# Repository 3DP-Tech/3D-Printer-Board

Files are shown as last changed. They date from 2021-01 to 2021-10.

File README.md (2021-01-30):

# 3D-Printer-Board
Check out my [3DP Tech You Tube channel](https://www.youtube.com/playlist?list=PLOfiVhkRK3Go6M8yRqPx5GOqqJWyXBp_2). This repository contains support files for the "Build a 3D Printer Control Board" series.

In this video series I explore the electronics of a 3D printer. I review the components that make up the control board and explain how they interact with the firmware to control a 3D printer. Finally, I show you how to build a complete control board for a 3D printer on a solderless breadboard.
## Episode Index
### Episode 1 - Introduction
In this episode I review the electronic components found in a 3D printer and give a high-level description of the role each plays to accomplish the task of printing a 3D model. I give an overview of the remaining episodes and state the objectives of the series.
### Episode 2 - Arduino Core
In this episode I demonstrate how to build a basic Arduino microcontroller on a breadboard. I guide you through the minimum circuit components required to get an ATMEGA1284P based Arduino up and running.
### Episode 3 - Flashing the Bootloader
In this episode I demonstrate how to flash a bootloader to the Arduino core circuit built in episode 2. This will allow firmware to be flashed easily from the Arduino IDE using a serial port.
### Episode 4 - Adding USB Support
In this episode I demonstrate a few ways to connect to the microcontroller using the USB port on a computer. I also demonstrate how to add a permanent USB port to the breadboard.
### Episode 5 - Power Supply
In this episode I demonstrate how to add a 5V regulator to the breadboard so that the control board can be run from a 12V or 24V power supply. I discuss the various ways to power the board while building it and cover the reason why a 12V or 24V power supply is necessary.
### Episode 6 - Stepper Motors
In this episode I review the basics of a stepper motor and demonstrate how to drive a stepper motor from an Arduino. I walk through adding the four necessary stepper motor drivers needed for the 3D printer.
### Episode 7 - Hot End, Bed Heater and Fan
In this episode I demonstrate how to control high voltage and high current devices through a MOSFET and an Arduino PWM pin. I discuss the basic principle of PWM and add the circuits to our breadboard that will control the fans, the hot bed heater the hot end heater cartridge.
### Episode 8 - Thermistors
In this episode I describe the basic operation of a thermistor and show how to read temperature. I walk through adding the necessary thermistor circuits to read temperatures on the 3D printer.
### Episode 9 - End Stops
In this episode I review the basics of monitoring a push button. I demonstrate how to add the end stop circuits to the printer control board.
### Episode 10 - LCD
In this episode I walk through the LCD used on the 3D printer and demonstrate how to add it to the control board.
### Episode 11 - Encoder & Piezo Buzzer
In this episode I demonstrate the basic function of the rotary encoder used to make menu selections on the LCD. I'll also show how to wire it into the breadboard along with the piezo buzzer (or beeper) to add (very) basic sound.
### Episode 12 - MicroSD Card
In this episode I demonstrate how to add a MicroSD card reader to the control board.
### Episode 13 - Flashing Marlin
In this episode I walk through configuring Marlin firmware for the control board and demonstrate how to flash it through the Arduino IDE. I also demonstrate the firmware operation on the control board using a virtual/demo 3D printer.
### Episode 14 - Connecting a Printer
In this episode I will connect the breadboard based control board to an actual 3D printer and print a 3D model.
### Episode 15 - Expanding the Board
In this episode I demonstrate ways to expand the board to offer more options that are readily supportable in the Marlin firmware.

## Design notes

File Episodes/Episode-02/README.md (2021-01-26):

# Episode 2 - Arduino Core
This folder contains supporting files for Episode 2.

## Arduino as ISP
Here is the reference to using the Arduino as a programmer.

[Arduino as ISP and Arduino Bootloaders](https://www.arduino.cc/en/pmwiki.php?n=Tutorial/ArduinoISP)

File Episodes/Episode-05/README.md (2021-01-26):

# Episode 5 - Power Supply
This folder contains supporting files for the episode.

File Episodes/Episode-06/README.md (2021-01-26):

# Episode 6 - Stepper Motors
This folder contains supporting files for the episode.

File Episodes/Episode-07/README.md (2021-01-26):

# Episode 7 - Hot End, Bed Heater and Fan
This folder contains supporting files for the episode.

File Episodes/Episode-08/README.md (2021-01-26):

# Episode 8 - Thermistors
This folder contains supporting files for the episode.

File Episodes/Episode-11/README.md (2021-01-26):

# Episode 11 - Encoder & Piezo Buzzer
This folder contains supporting files for the episode.

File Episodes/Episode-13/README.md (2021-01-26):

# Episode 13 - Flashing Marlin
This folder contains supporting files for the episode.

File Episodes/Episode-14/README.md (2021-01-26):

# Episode 14 - Connecting a Printer
This folder contains supporting files for the episode.

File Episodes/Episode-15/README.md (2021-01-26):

# Episode 15 - Expanding the Board
This folder contains supporting files for the episode.

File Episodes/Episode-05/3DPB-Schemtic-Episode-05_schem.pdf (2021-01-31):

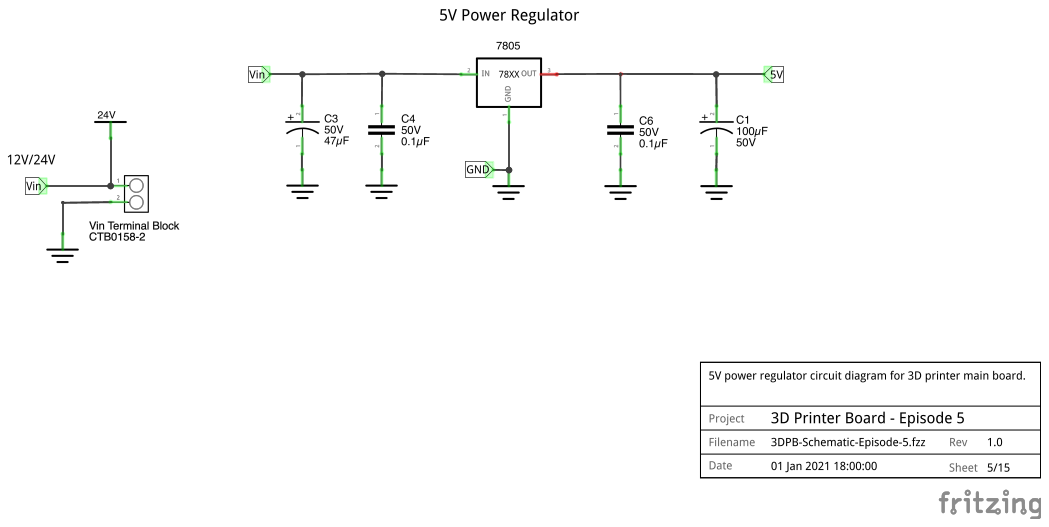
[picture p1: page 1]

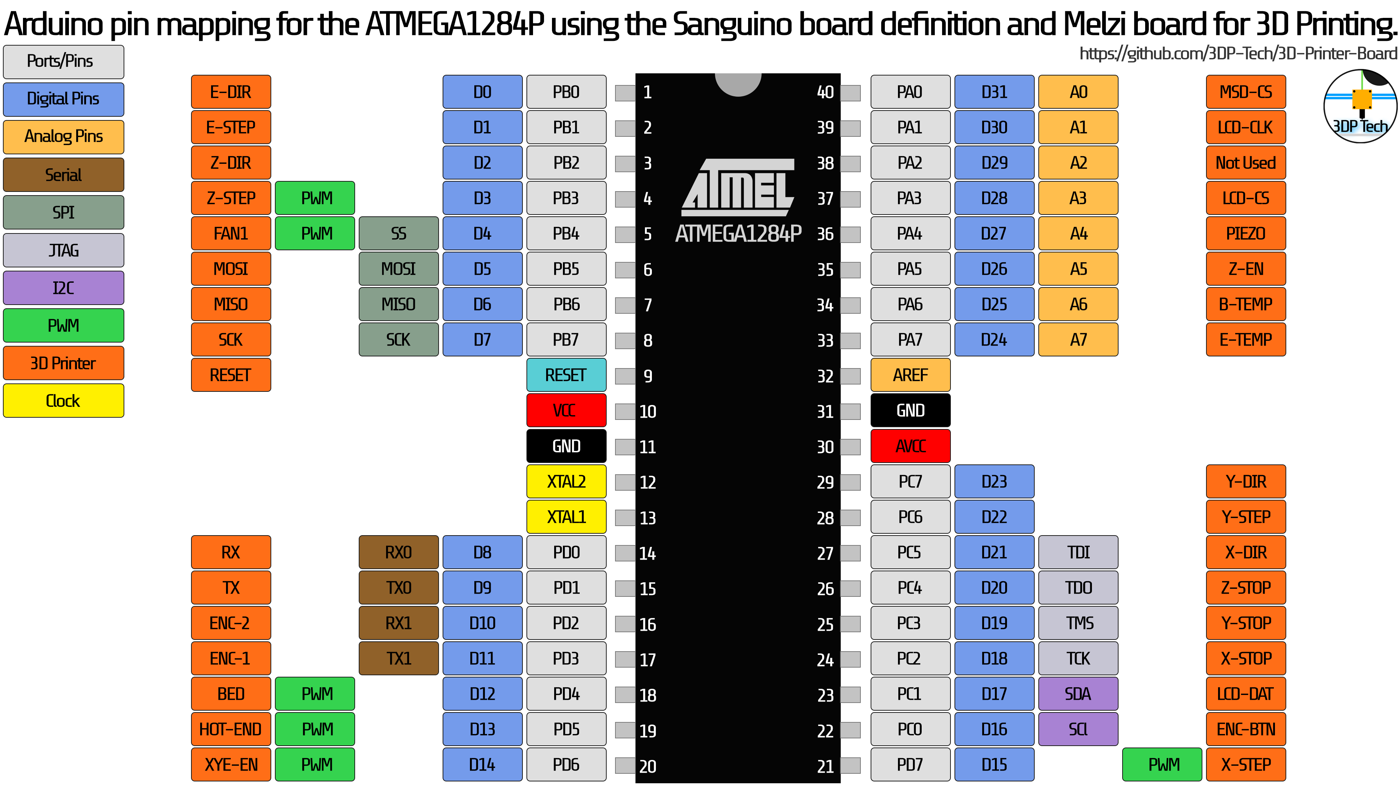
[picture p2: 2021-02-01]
Extras/ATMega1284P-Pins.png

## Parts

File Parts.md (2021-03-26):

# Obtaining Parts and Tools
The products used in this episode are listed below along with at least one source link.

Hopefully you have much of the items on this list already. If you try to purchase everything the cost will be very high. I include the complete list of items I use but I also show ways to get around not having some of these items.

> All parts that are referenced from Adafruit can be ordered directly from this list:
> [Adafruit Wishlist](http://www.adafruit.com/wishlists/517409)

> All of the parts referenced from Amazon can be ordered directly from this list:  [Amazon Wishlist](https://www.amazon.com/ideas/amzn1.account.AHJPQKIYOSU7VLCNUL2MLWOG4RNA/3R3GTU77Y6I2H)

# Parts List and Source
## All Episodes
### Tools
There are a couple of tools that are necessary. A pair of side/diagonal cutters, a pair of wire strippers and a pair of needle-nose pliers. Optionally you may need a soldering iron. I highly recommend a good one, but there are so many to choose from. Below are links to recommended products but you can find suitable alternatives if you like.

* [Flush diagonal cutters](https://www.adafruit.com/product/527)
* [Wire Strippers](https://www.adafruit.com/product/527)
* [Simple pliers](https://www.adafruit.com/product/527)
* [Digital Genuine Hakko FX-888D](https://www.adafruit.com/product/527)

### Large Solderless Breadboard
The large board I am using was purchased from Adafruit ([https://www.adafruit.com/product/443](https://www.adafruit.com/product/443)). If you do not want to purchase this board, or you already have some breadboards, you can just take three breadboards and lock them together. Good quality boards can be purchased from Amazon as well ([https://www.amazon.com/gp/product/B07FY9LQJF](https://www.amazon.com/gp/product/B07FY9LQJF)).

### Hook-up Wire Spool Set
It is nice to have a set of hook-up wire suitable for a breadboard. In the videos I cut most of the wires to length to keep the board neat and clean. 

This is solid core wire (22AWG Solid Core - 6 x 25 ft) and can be purchased from Adafruit ([https://www.adafruit.com/product/131](https://www.adafruit.com/product/1311)1), or from Amazon ([https://www.amazon.com/gp/product/B00B4ZRPEY](https://www.amazon.com/gp/product/B00B4ZRPEY)).

### Jumper Wires
In addition to cutting wires to length, it is useful to have a few pre-made jumper wires. These wll come in handy for working with the Uno to program the chip or to connect the power supply.

[https://www.adafruit.com/product/1957](https://www.adafruit.com/product/1957)
## Episode 1
No parts needed for this episode.
## Episode 2
### Adjustable Power Supply
I am using a bench top adjustable power supply for to power my mainboard through most of the episodes. There are many varieties of these at a range of prices. The power supply I am using in the videos is linked below.

[https://www.amazon.com/gp/product/B085S34NNW](https://www.amazon.com/gp/product/B085S34NNW)

### Arduino Uno
An AVR programmer is required to program the ATMEGA1284P and to load a bootloader. It is much easier to use an Arduino. The simplest board to use for this is the Uno but any 5V Arduino board will work.

[https://store.arduino.cc/usa/arduino-uno-rev3]()

### ATMEGA1284P
I ordered this directly from Microchip. The shipping was low, and it came in a few days. I recommend ordering at least 2 since these are only a few dollars.

[https://www.microchipdirect.com/product/ATMEGA1284P-PU](https://www.microchipdirect.com/product/ATMEGA1284P-PU)

### Clock Crystal
The ATMEGA1284P will be run using a 16Mhz crystal. The datasheet also calls for two 20pF capacitors. These three parts can be purchased from Adafruit in a kit.

[https://www.adafruit.com/product/2215](https://www.adafruit.com/product/2215)

### Breadboard Compatible Tactile Push Button
Adafruit sells a pack of these buttons that can be pressed into the breadboard. This package includes snap on buttons that make it easy to use the switch.

[https://www.adafruit.com/product/1009](https://www.adafruit.com/product/1009)

### 6-pin AVR ISP Breadboard Adapter
These are not required but make programming the ATMEGA1284 bootloader a little easier (and they help make the wiring easier). I recommend ordering two of these.

[https://www.adafruit.com/product/1465](https://www.adafruit.com/product/1465)

### 6-pin Socket/Socket IDC cable - 6"
This is the companion cable to the AVR ISP breadboard adapter above.

[https://www.adafruit.com/product/371](https://www.adafruit.com/product/371)

### Breadboard-friendly SPDT Slide Switch
This is optional, but this slide switch can be added to the breadboard as a power switch.

[https://www.adafruit.com/product/805](https://www.adafruit.com/product/805)

### Mini Digital DC Voltmeter
I use these to monitor the voltage on the breadboard. They are also handy to measure the output of the MOSFETs.

[https://www.amazon.com/gp/product/B0761MG9NS](https://www.amazon.com/gp/product/B0761MG9NS)

### Resistors
Resistors can be purchased up from just about anywhere. Either purchase them by size or get a variety container from Amazon (https://www.amazon.com/gp/product/B08BNDL6DS).

**Sizes Needed:**
220 Ω, 10K Ω

### Capacitors
Capacitors can be purchased from just about anywhere. Either purchase them by size or get a variety container from Amazon (https://www.amazon.com/gp/product/B08BNDL6DS).

Electrolytic: [https://www.amazon.com/gp/product/B07TWCT2ZB](https://www.amazon.com/gp/product/B07TWCT2ZB)

**Sizes needed:**
10 µF, 47 µF, 100 µF

Ceramic: [https://www.amazon.com/gp/product/B07TWBVJVN](https://www.amazon.com/gp/product/B07TWBVJVN)

**Sizes needed:**
0.1 µF, 20 pF (if you purchase the crystal without them)

### LEDs
Multiple LEDs in a variety of colors are used. It does not matter if you use the 3mm or 5mm size. I recommend at least three colors, red, green and blue. LEDs can be purchased on varitey packs or by color.

* [Diffused 5mm LED Pack - 5 LEDs each in 5 Colors - 25 Pack](https://www.adafruit.com/product/4203)
* [Super Bright Red 5mm LED (25 pack)](https://www.adafruit.com/product/297)
* [Super Bright Green 5mm LED (25 pack)](https://www.adafruit.com/product/300)
* [Super Bright Blue 5mm LED (25 pack)](https://www.adafruit.com/product/301)

## Episode 12

### Rotary Encoder
https://www.adafruit.com/product/377

### Fancy Knob
(very optional)
https://www.adafruit.com/product/2056

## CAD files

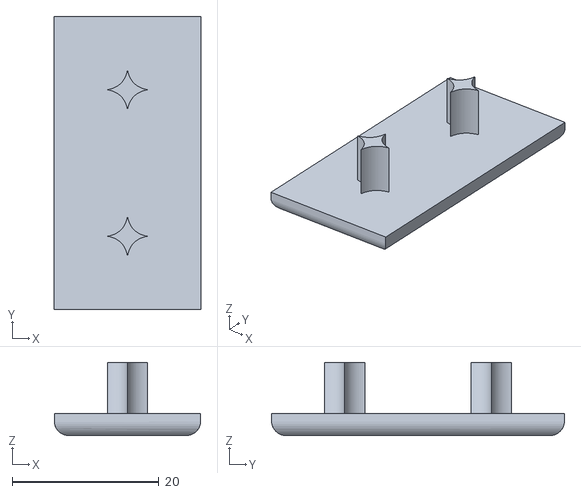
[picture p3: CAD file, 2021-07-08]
STL/Mj_End_Cap_with_pins.stl
20.0 x 40.0 x 10.0

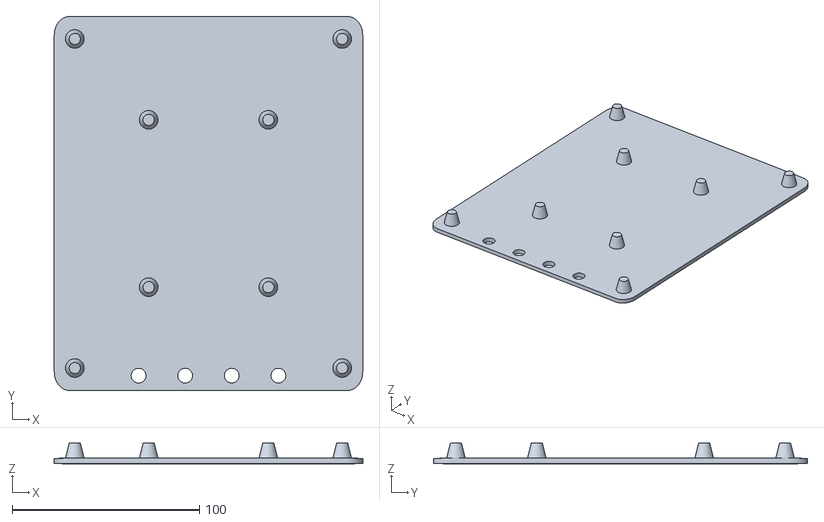
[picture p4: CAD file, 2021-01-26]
STL/Large-Breadboard-Plate.stl
165.0 x 200.0 x 11.0

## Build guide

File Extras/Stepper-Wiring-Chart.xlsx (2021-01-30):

Connector
Red | Black | Blue | Green
A | B | C | D
B+ | A+ | B- | A-
1B | 2B | 1A | 2A
Pair 1 | Pair 2 | Pair 1 | Pair 2

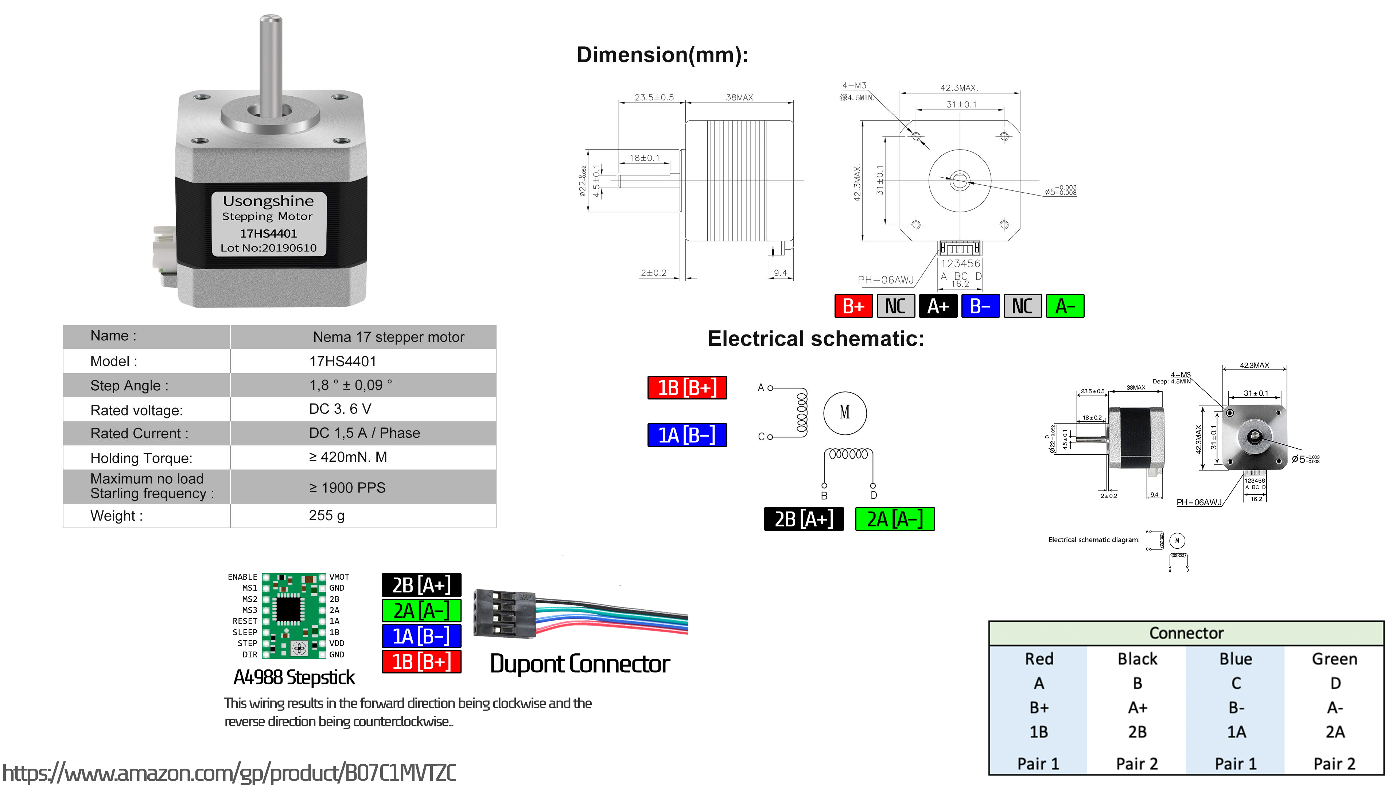
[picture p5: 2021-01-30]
Extras/Stepper-Wiring.png

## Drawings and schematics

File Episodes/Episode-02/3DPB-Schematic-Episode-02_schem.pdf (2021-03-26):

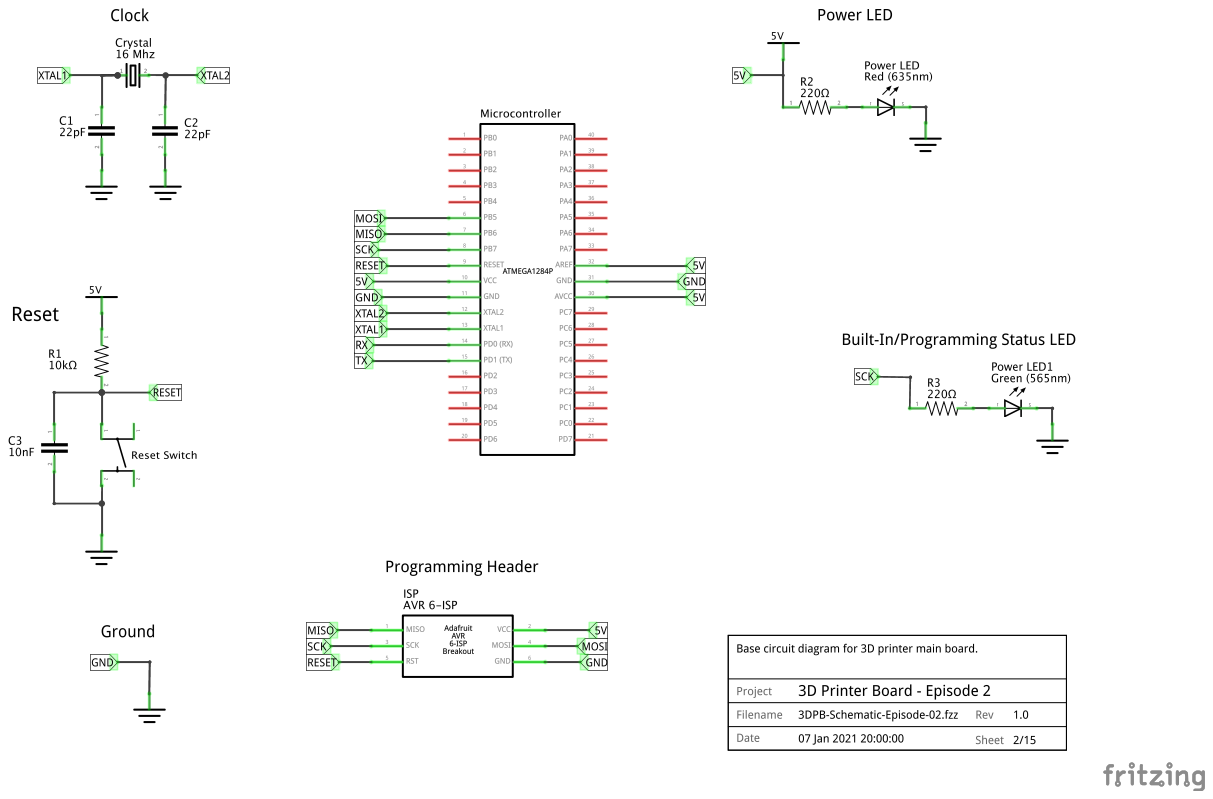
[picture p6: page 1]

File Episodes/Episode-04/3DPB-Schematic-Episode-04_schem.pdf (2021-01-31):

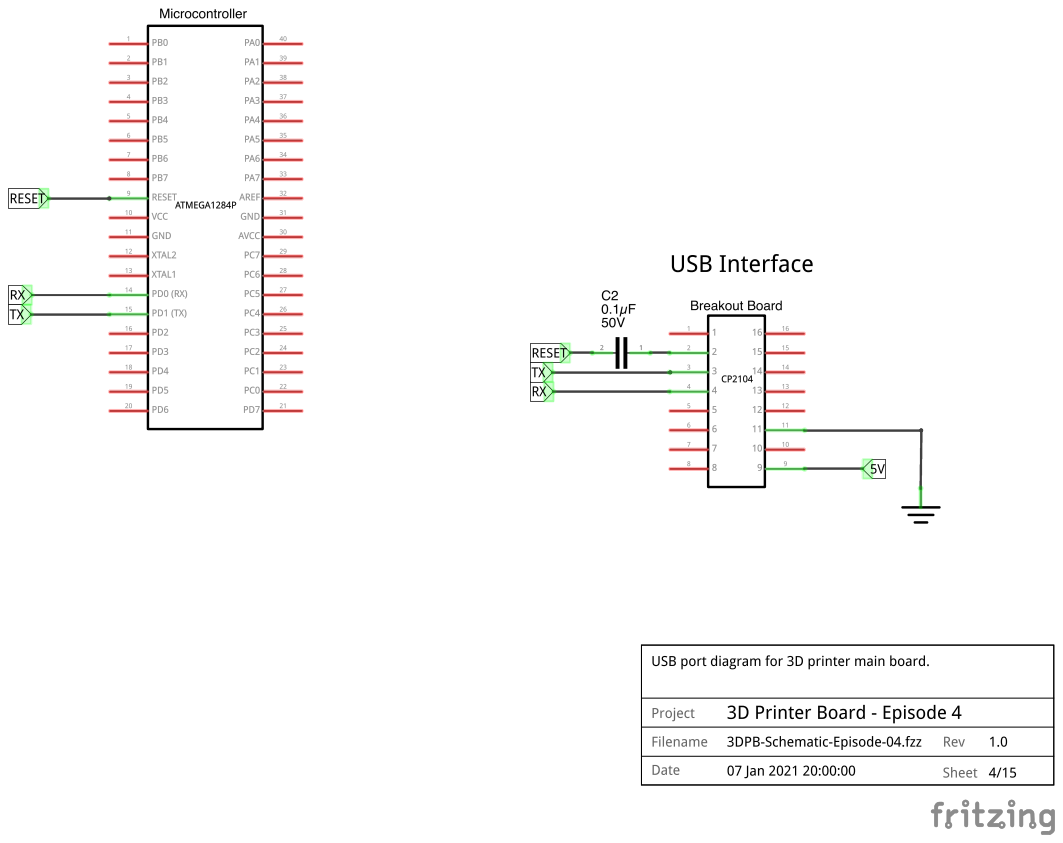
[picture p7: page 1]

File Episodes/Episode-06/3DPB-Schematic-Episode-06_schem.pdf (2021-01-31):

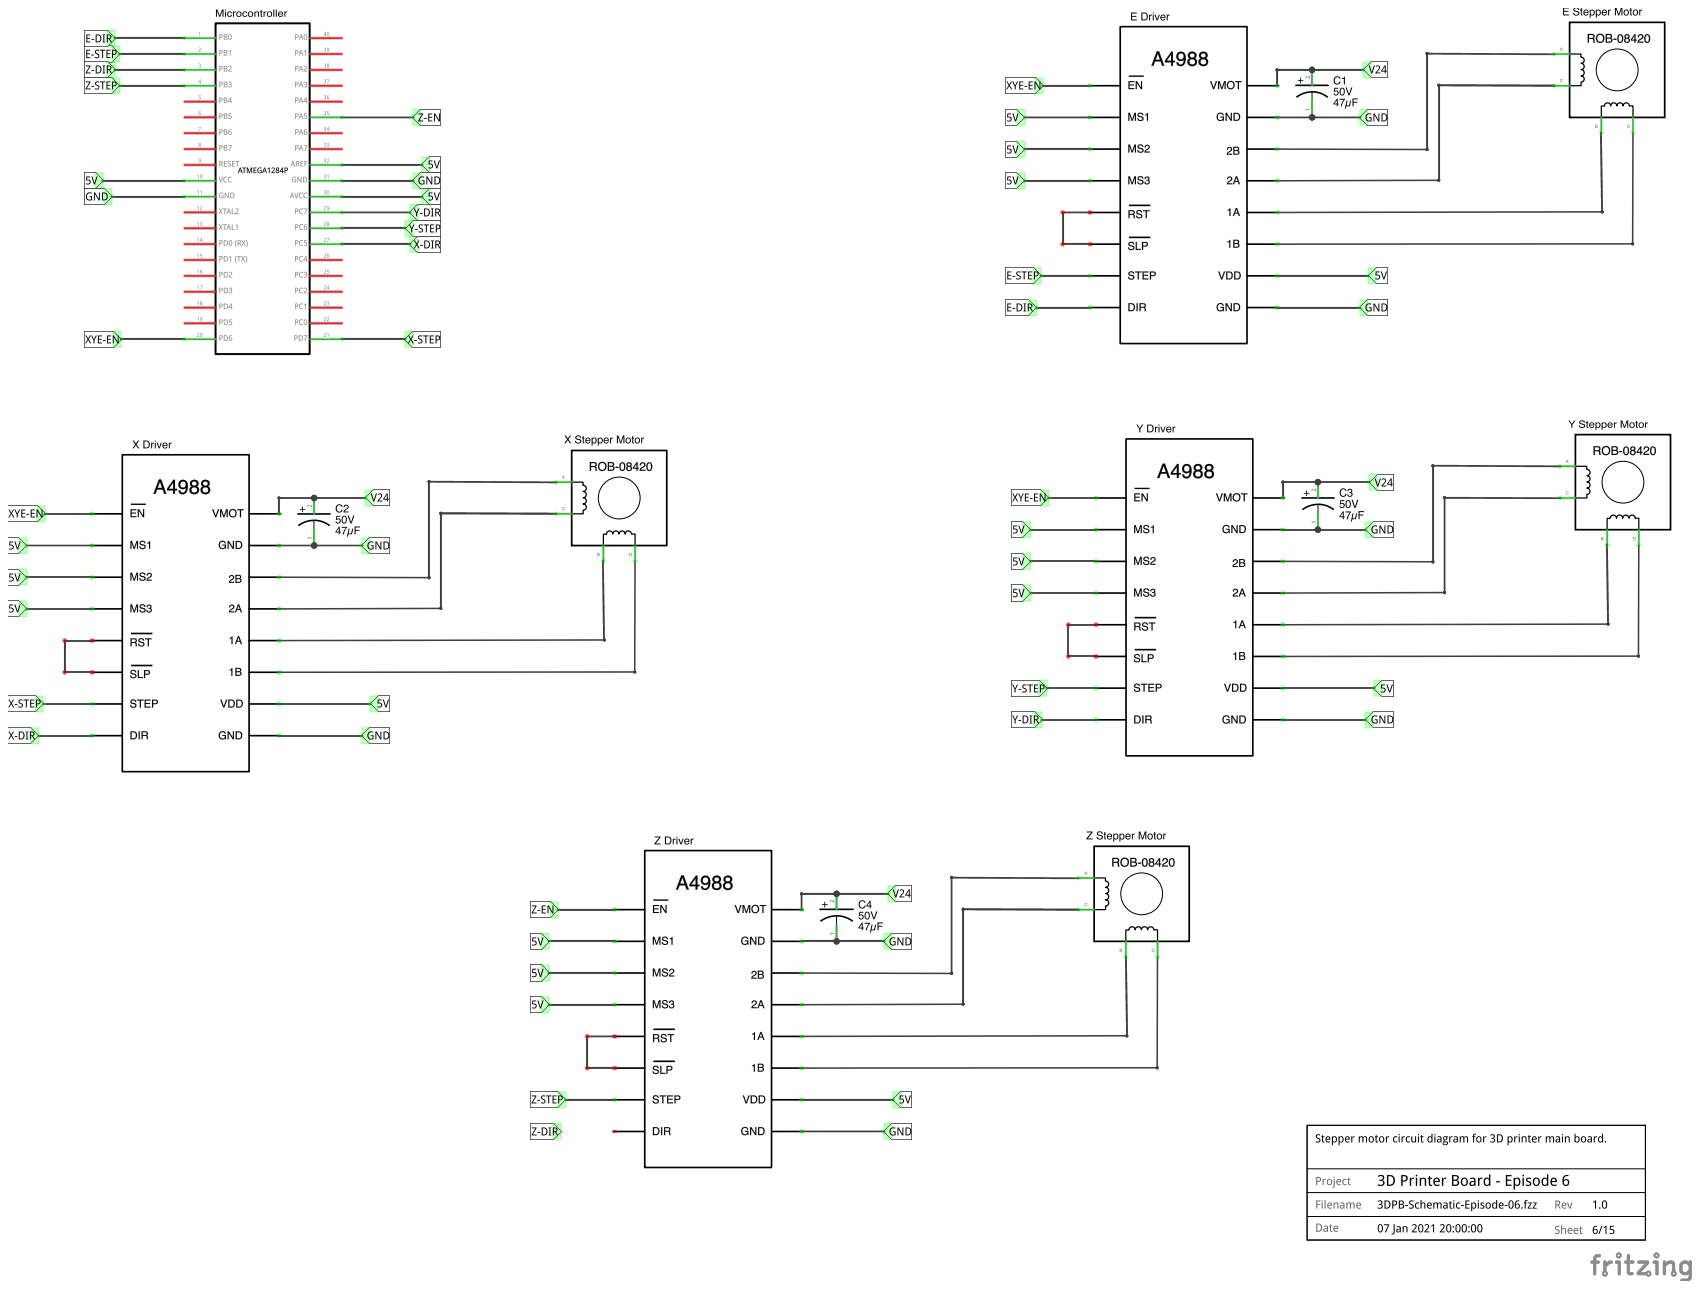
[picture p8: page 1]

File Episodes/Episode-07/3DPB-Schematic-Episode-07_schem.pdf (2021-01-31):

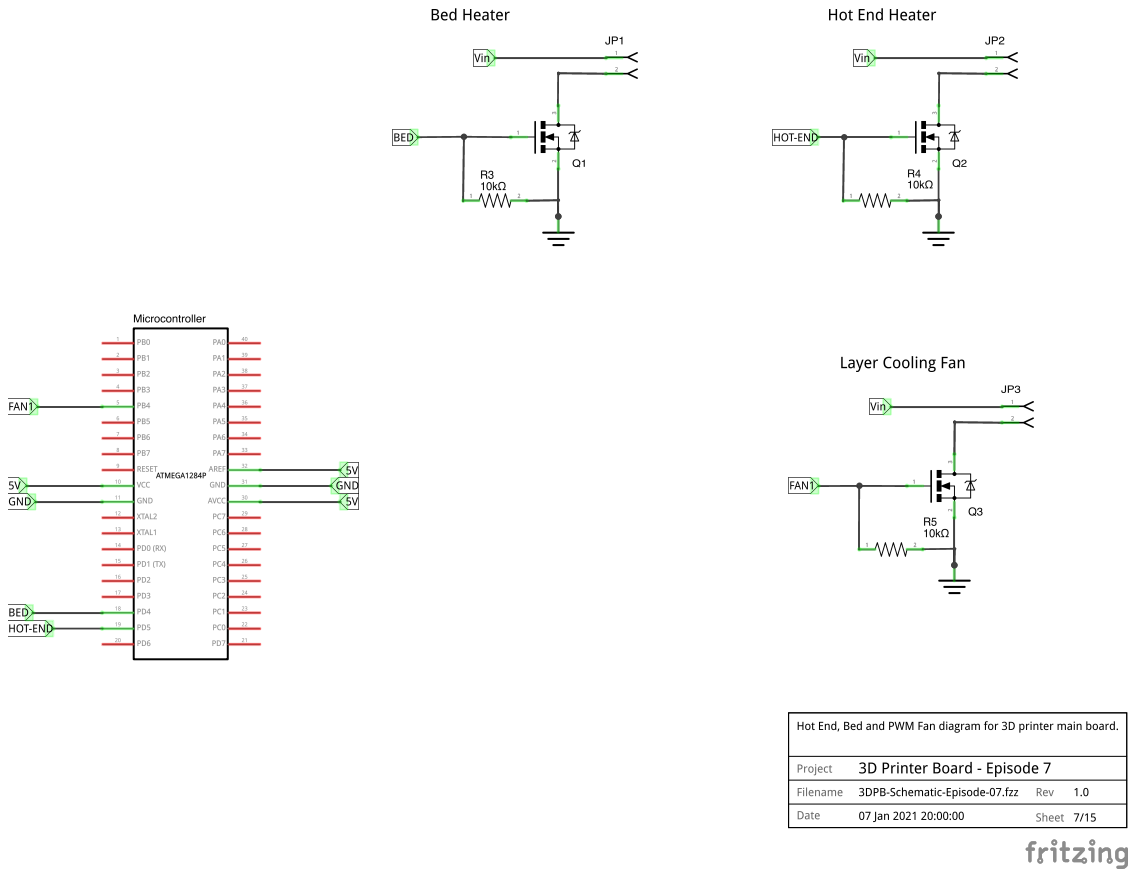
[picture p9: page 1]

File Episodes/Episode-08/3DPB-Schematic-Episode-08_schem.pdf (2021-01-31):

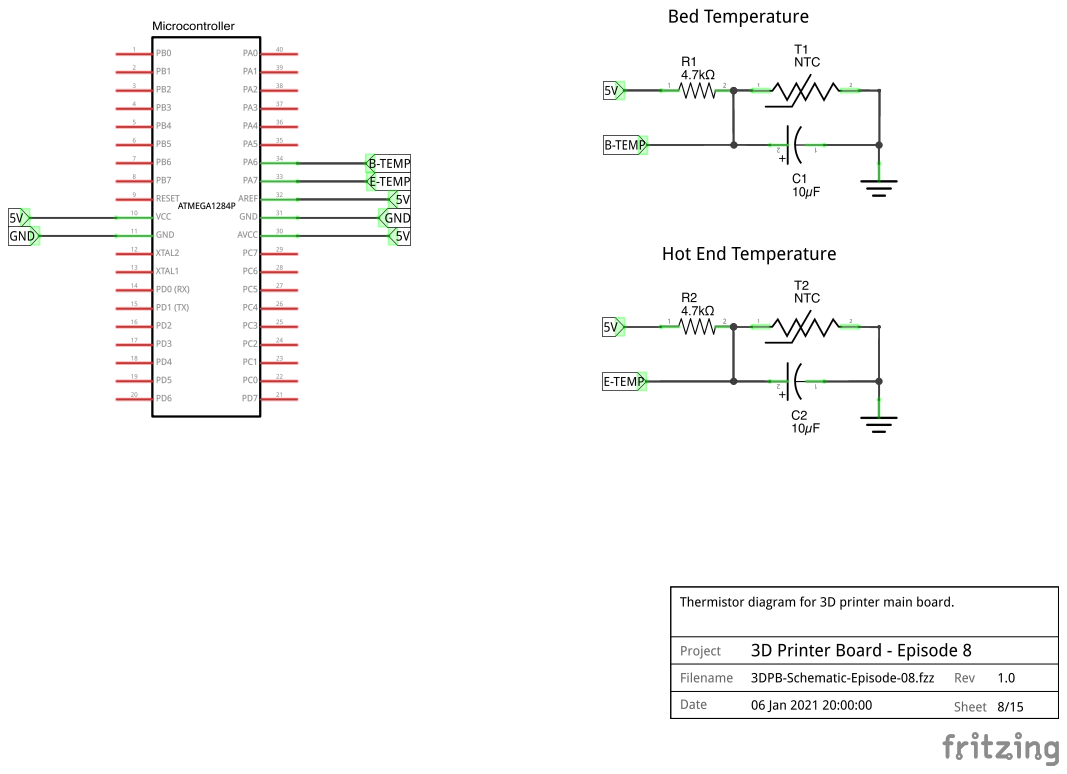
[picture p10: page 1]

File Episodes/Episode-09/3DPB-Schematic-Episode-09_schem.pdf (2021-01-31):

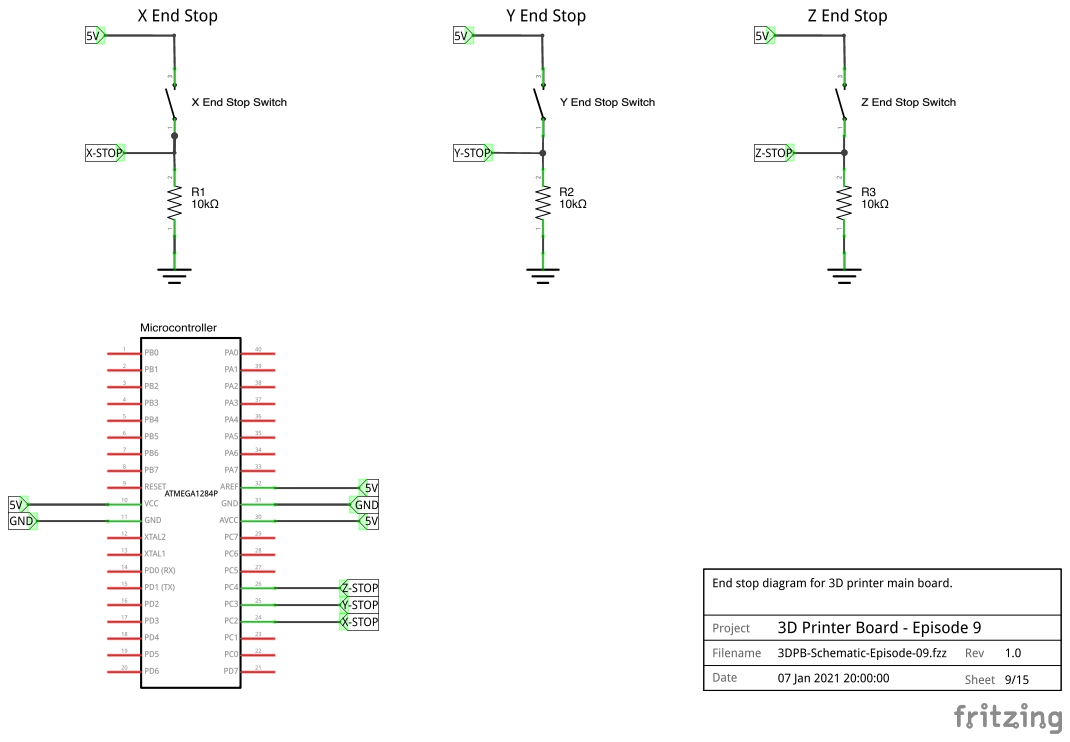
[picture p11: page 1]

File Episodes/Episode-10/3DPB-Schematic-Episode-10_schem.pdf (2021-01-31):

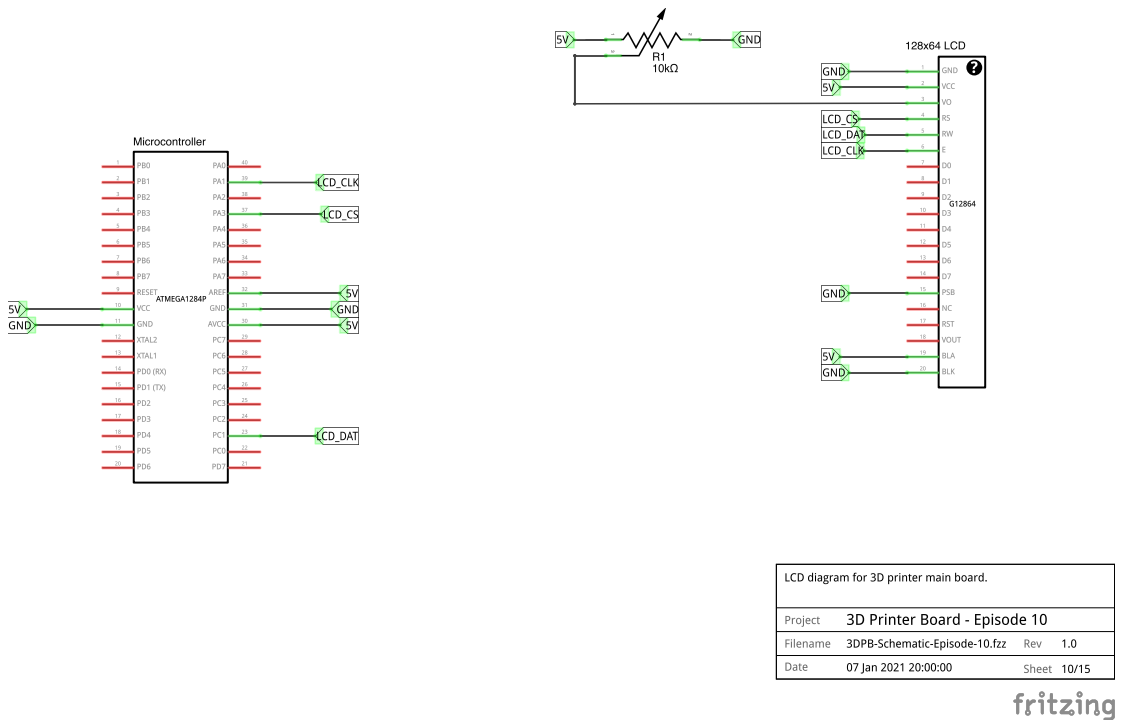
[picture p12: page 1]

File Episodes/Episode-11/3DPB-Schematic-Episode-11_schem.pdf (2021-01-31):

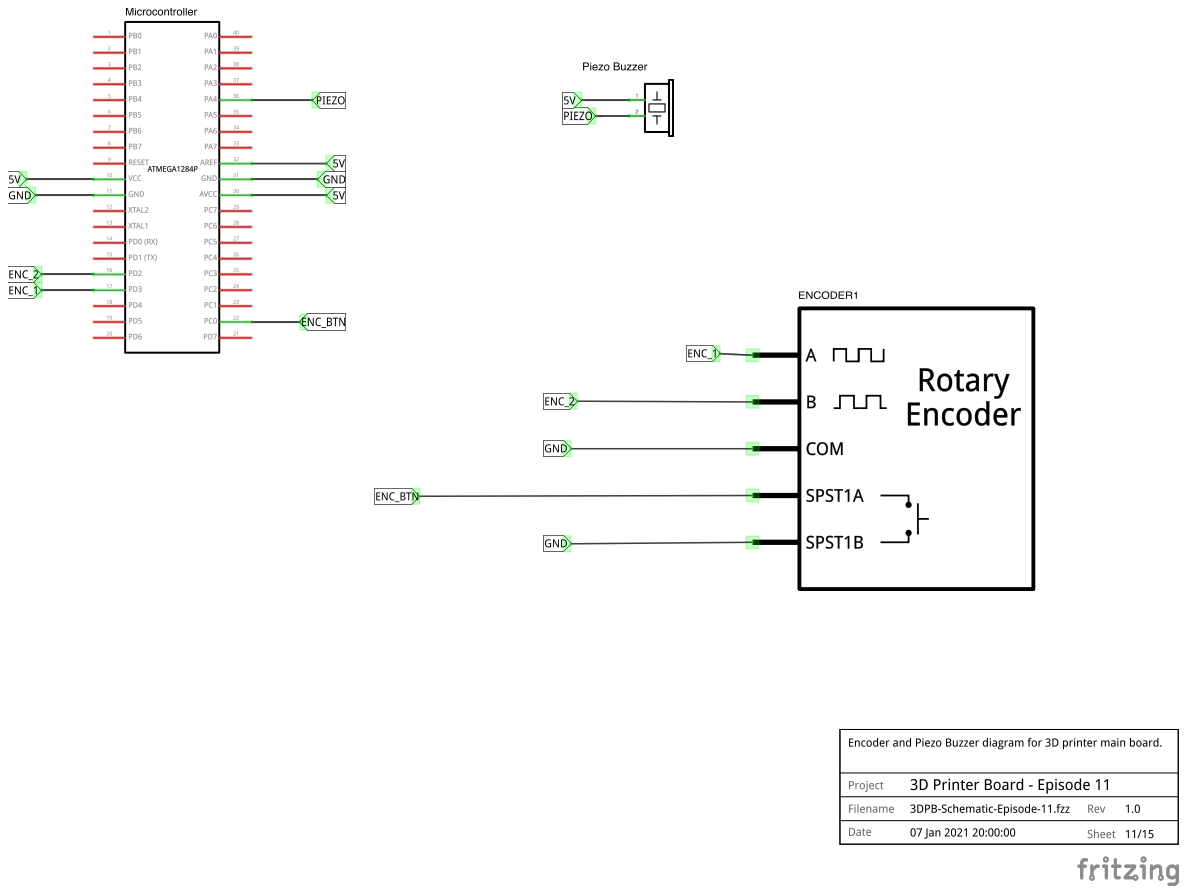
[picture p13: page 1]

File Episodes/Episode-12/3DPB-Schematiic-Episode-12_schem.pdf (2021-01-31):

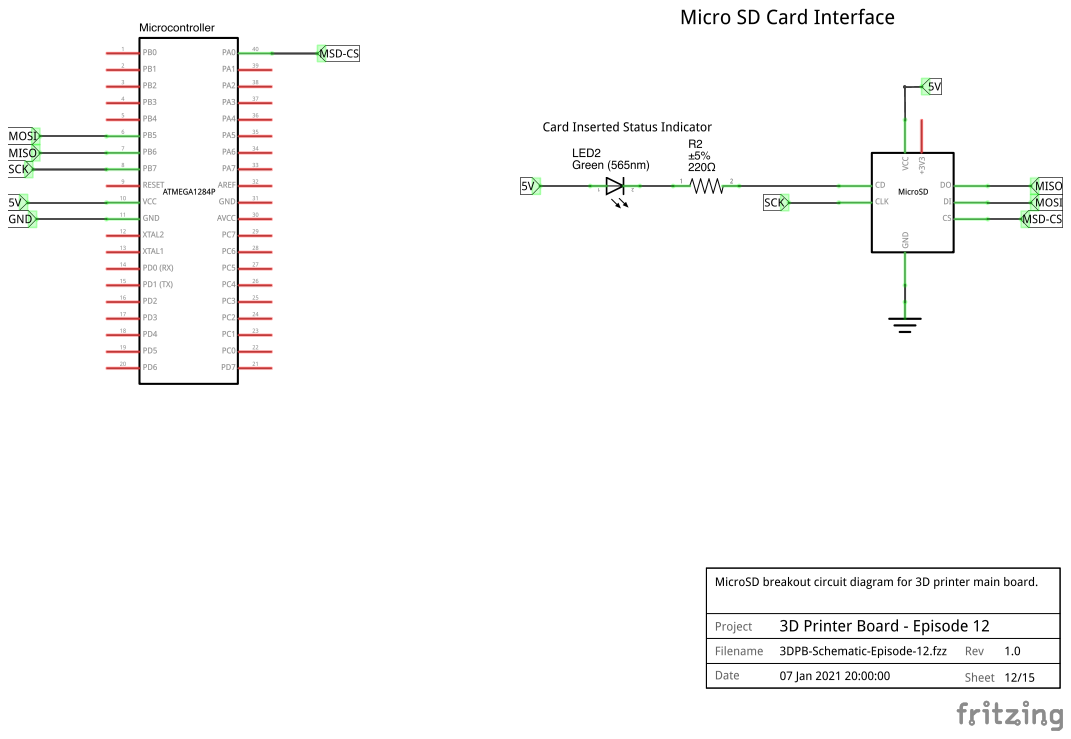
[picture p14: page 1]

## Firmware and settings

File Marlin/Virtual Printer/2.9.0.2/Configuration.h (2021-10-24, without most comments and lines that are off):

#pragma once
#define CONFIGURATION_H_VERSION 02000902
#define STRING_CONFIG_H_AUTHOR "(Daniel Porrey, 3DP-Tech)" // Who made the changes.
#define SHOW_BOOTSCREEN
#define SHOW_CUSTOM_BOOTSCREEN
#define CUSTOM_STATUS_SCREEN_IMAGE
#define SERIAL_PORT 0
#define BAUDRATE 500000
  #define MOTHERBOARD BOARD_MELZI_CREALITY
#define CUSTOM_MACHINE_NAME "V3D Printer"
#define MACHINE_UUID "3f756d04-a356-4632-ac29-15a5529378b4"
#if LINEAR_AXES >= 4
  #define AXIS4_NAME 'A' // :['A', 'B', 'C', 'U', 'V', 'W']
#endif
#if LINEAR_AXES >= 5
  #define AXIS5_NAME 'B' // :['A', 'B', 'C', 'U', 'V', 'W']
#endif
#if LINEAR_AXES >= 6
  #define AXIS6_NAME 'C' // :['A', 'B', 'C', 'U', 'V', 'W']
#endif
#define EXTRUDERS 1
#define DEFAULT_NOMINAL_FILAMENT_DIA 1.75
#define TEMP_SENSOR_0 1
#define TEMP_SENSOR_1 0
#define TEMP_SENSOR_2 0
#define TEMP_SENSOR_3 0
#define TEMP_SENSOR_4 0
#define TEMP_SENSOR_5 0
#define TEMP_SENSOR_6 0
#define TEMP_SENSOR_7 0
#define TEMP_SENSOR_BED 1
#define TEMP_SENSOR_PROBE 0
#define TEMP_SENSOR_CHAMBER 0
#define TEMP_SENSOR_COOLER 0
#define TEMP_SENSOR_BOARD 0
#define TEMP_SENSOR_REDUNDANT 0
#define DUMMY_THERMISTOR_998_VALUE  25
#define DUMMY_THERMISTOR_999_VALUE 100
#define TEMP_RESIDENCY_TIME         10  // (seconds) Time to wait for hotend to "settle" in M109
#define TEMP_WINDOW                  1  // (°C) Temperature proximity for the "temperature reached" timer
#define TEMP_HYSTERESIS              3  // (°C) Temperature proximity considered "close enough" to the target
#define TEMP_BED_RESIDENCY_TIME     10  // (seconds) Time to wait for bed to "settle" in M190
#define TEMP_BED_WINDOW              1  // (°C) Temperature proximity for the "temperature reached" timer
#define TEMP_BED_HYSTERESIS          3  // (°C) Temperature proximity considered "close enough" to the target
#define TEMP_CHAMBER_RESIDENCY_TIME 10  // (seconds) Time to wait for chamber to "settle" in M191
#define TEMP_CHAMBER_WINDOW          1  // (°C) Temperature proximity for the "temperature reached" timer
#define TEMP_CHAMBER_HYSTERESIS      3  // (°C) Temperature proximity considered "close enough" to the target
#if TEMP_SENSOR_REDUNDANT
  #define TEMP_SENSOR_REDUNDANT_SOURCE    E1  // The sensor that will provide the redundant reading.
  #define TEMP_SENSOR_REDUNDANT_TARGET    E0  // The sensor that we are providing a redundant reading for.
  #define TEMP_SENSOR_REDUNDANT_MAX_DIFF  10  // (°C) Temperature difference that will trigger a print abort.
#endif
#define HEATER_0_MINTEMP   5
#define HEATER_1_MINTEMP   5
#define HEATER_2_MINTEMP   5
#define HEATER_3_MINTEMP   5
#define HEATER_4_MINTEMP   5
#define HEATER_5_MINTEMP   5
#define HEATER_6_MINTEMP   5
#define HEATER_7_MINTEMP   5
#define BED_MINTEMP        5
#define CHAMBER_MINTEMP    5
#define HEATER_0_MAXTEMP 275
#define HEATER_1_MAXTEMP 275
#define HEATER_2_MAXTEMP 275
#define HEATER_3_MAXTEMP 275
#define HEATER_4_MAXTEMP 275
#define HEATER_5_MAXTEMP 275
#define HEATER_6_MAXTEMP 275
#define HEATER_7_MAXTEMP 275
#define BED_MAXTEMP      125
#define CHAMBER_MAXTEMP  60
#define HOTEND_OVERSHOOT 15   // (°C) Forbid temperatures over MAXTEMP - OVERSHOOT
#define BED_OVERSHOOT    10   // (°C) Forbid temperatures over MAXTEMP - OVERSHOOT
#define COOLER_OVERSHOOT  2   // (°C) Forbid temperatures closer than OVERSHOOT
#define PIDTEMP
#define BANG_MAX 255     // Limits current to nozzle while in bang-bang mode; 255=full current
#define PID_MAX BANG_MAX // Limits current to nozzle while PID is active (see PID_FUNCTIONAL_RANGE below); 255=full current
#define PID_K1 0.95      // Smoothing factor within any PID loop
  #define PID_EDIT_MENU         // Add PID editing to the "Advanced Settings" menu. (~700 bytes of PROGMEM)
  #define PID_AUTOTUNE_MENU     // Add PID auto-tuning to the "Advanced Settings" menu. (~250 bytes of PROGMEM)
    #define DEFAULT_Kp  22.20
    #define DEFAULT_Ki   1.08
    #define DEFAULT_Kd 114.00
#define PIDTEMPBED
#define MAX_BED_POWER 255 // limits duty cycle to bed; 255=full current
  #define DEFAULT_bedKp 10.00
  #define DEFAULT_bedKi .023
  #define DEFAULT_bedKd 305.4
#define MAX_CHAMBER_POWER 255 // limits duty cycle to chamber heater; 255=full current
  #define PID_FUNCTIONAL_RANGE 10 // If the temperature difference between the target temperature and the actual temperature
#define EXTRUDE_MINTEMP 170
#define EXTRUDE_MAXLENGTH 200
#define THERMAL_PROTECTION_HOTENDS // Enable thermal protection for all extruders
#define THERMAL_PROTECTION_BED     // Enable thermal protection for the heated bed
#define THERMAL_PROTECTION_CHAMBER // Enable thermal protection for the heated chamber
#define THERMAL_PROTECTION_COOLER  // Enable thermal protection for the laser cooling
#define USE_XMIN_PLUG
#define USE_YMIN_PLUG
#define USE_ZMIN_PLUG
#define ENDSTOPPULLUPS
#define X_MIN_ENDSTOP_INVERTING false // Set to true to invert the logic of the endstop.
#define Y_MIN_ENDSTOP_INVERTING false // Set to true to invert the logic of the endstop.
#define Z_MIN_ENDSTOP_INVERTING false // Set to true to invert the logic of the endstop.
#define I_MIN_ENDSTOP_INVERTING false // Set to true to invert the logic of the endstop.
#define J_MIN_ENDSTOP_INVERTING false // Set to true to invert the logic of the endstop.
#define K_MIN_ENDSTOP_INVERTING false // Set to true to invert the logic of the endstop.
#define X_MAX_ENDSTOP_INVERTING false // Set to true to invert the logic of the endstop.
#define Y_MAX_ENDSTOP_INVERTING false // Set to true to invert the logic of the endstop.
#define Z_MAX_ENDSTOP_INVERTING false // Set to true to invert the logic of the endstop.
#define I_MAX_ENDSTOP_INVERTING false // Set to true to invert the logic of the endstop.
#define J_MAX_ENDSTOP_INVERTING false // Set to true to invert the logic of the endstop.
#define K_MAX_ENDSTOP_INVERTING false // Set to true to invert the logic of the endstop.
#define Z_MIN_PROBE_ENDSTOP_INVERTING false // Set to true to invert the logic of the probe.
#define X_DRIVER_TYPE  A4988
#define Y_DRIVER_TYPE  A4988
#define Z_DRIVER_TYPE  A4988
#define E0_DRIVER_TYPE A4988
#define DEFAULT_AXIS_STEPS_PER_UNIT   { 400, 400, 400, 93 }
#define DEFAULT_MAX_FEEDRATE          { 100, 100, 100, 100 }
#define DEFAULT_MAX_ACCELERATION      { 500, 500, 500, 500 }
#define DEFAULT_ACCELERATION          500    // X, Y, Z and E acceleration for printing moves
#define DEFAULT_RETRACT_ACCELERATION  500    // E acceleration for retracts
#define DEFAULT_TRAVEL_ACCELERATION   500    // X, Y, Z acceleration for travel (non printing) moves
#define DEFAULT_EJERK    5.0  // May be used by Linear Advance
  #define JUNCTION_DEVIATION_MM 0.08  // (mm) Distance from real junction edge
  #define JD_HANDLE_SMALL_SEGMENTS    // Use curvature estimation instead of just the junction angle
#define Z_MIN_PROBE_USES_Z_MIN_ENDSTOP_PIN
#define NOZZLE_TO_PROBE_OFFSET { 10, 10, 0 }
#define PROBING_MARGIN 10
#define XY_PROBE_FEEDRATE (133*60)
#define Z_PROBE_FEEDRATE_FAST (4*60)
#define Z_PROBE_FEEDRATE_SLOW (Z_PROBE_FEEDRATE_FAST / 2)
#define Z_CLEARANCE_DEPLOY_PROBE   10 // Z Clearance for Deploy/Stow
#define Z_CLEARANCE_BETWEEN_PROBES  5 // Z Clearance between probe points
#define Z_CLEARANCE_MULTI_PROBE     5 // Z Clearance between multiple probes
#define Z_PROBE_LOW_POINT          -2 // Farthest distance below the trigger-point to go before stopping
#define Z_PROBE_OFFSET_RANGE_MIN -20
#define Z_PROBE_OFFSET_RANGE_MAX 20
#define X_ENABLE_ON 0
#define Y_ENABLE_ON 0
#define Z_ENABLE_ON 0
#define E_ENABLE_ON 0 // For all extruders
#define DISABLE_X false
#define DISABLE_Y false
#define DISABLE_Z false
#define DISABLE_E false             // Disable the extruder when not stepping
#define DISABLE_INACTIVE_EXTRUDER   // Keep only the active extruder enabled
#define INVERT_X_DIR true
#define INVERT_Y_DIR false
#define INVERT_Z_DIR false
#define INVERT_E0_DIR true
#define INVERT_E1_DIR false
#define INVERT_E2_DIR false
#define INVERT_E3_DIR false
#define INVERT_E4_DIR false
#define INVERT_E5_DIR false
#define INVERT_E6_DIR false
#define INVERT_E7_DIR false
#define X_HOME_DIR -1
#define Y_HOME_DIR -1
#define Z_HOME_DIR -1
#define X_BED_SIZE 160
#define Y_BED_SIZE 200
#define X_MIN_POS 0
#define Y_MIN_POS 0
#define Z_MIN_POS 0
#define X_MAX_POS X_BED_SIZE
#define Y_MAX_POS Y_BED_SIZE
#define Z_MAX_POS 260
#define MIN_SOFTWARE_ENDSTOPS
  #define MIN_SOFTWARE_ENDSTOP_X
  #define MIN_SOFTWARE_ENDSTOP_Y
  #define MIN_SOFTWARE_ENDSTOP_Z
  #define MIN_SOFTWARE_ENDSTOP_I
  #define MIN_SOFTWARE_ENDSTOP_J
  #define MIN_SOFTWARE_ENDSTOP_K
#define MAX_SOFTWARE_ENDSTOPS
  #define MAX_SOFTWARE_ENDSTOP_X
  #define MAX_SOFTWARE_ENDSTOP_Y
  #define MAX_SOFTWARE_ENDSTOP_Z
  #define MAX_SOFTWARE_ENDSTOP_I
  #define MAX_SOFTWARE_ENDSTOP_J
  #define MAX_SOFTWARE_ENDSTOP_K
  #define SOFT_ENDSTOPS_MENU_ITEM  // Enable/Disable software endstops from the LCD
#define HOMING_FEEDRATE_MM_M { (20*60), (20*60), (20*60) }
#define VALIDATE_HOMING_ENDSTOPS
#define EEPROM_SETTINGS     // Persistent storage with M500 and M501
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

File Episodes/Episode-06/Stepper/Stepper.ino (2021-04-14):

/*
  MIT License
  
  Copyright (c) 2021 Daniel Porrey
  
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
  THE SOFTWARE IS PROVIDED "AS IS", WITHOUT WARRANTY OF ANY KIND, EXPRESS OR
  IMPLIED, INCLUDING BUT NOT LIMITED TO THE WARRANTIES OF MERCHANTABILITY,
  FITNESS FOR A PARTICULAR PURPOSE AND NONINFRINGEMENT. IN NO EVENT SHALL THE
  AUTHORS OR COPYRIGHT HOLDERS BE LIABLE FOR ANY CLAIM, DAMAGES OR OTHER
  LIABILITY, WHETHER IN AN ACTION OF CONTRACT, TORT OR OTHERWISE, ARISING FROM,
  OUT OF OR IN CONNECTION WITH THE SOFTWARE OR THE USE OR OTHER DEALINGS IN THE
  SOFTWARE.
*/
#include <SpeedyStepper.h>

//
// Uncomment one of the lines below to select 
// the motor connection.
//
//#define E-MOTOR
//#define Z-MOTOR
#define X-MOTOR
//#define Y-MOTOR

#include "MotorPins.h"

//*****************************************************
//*****************************************************
// Motor Wiring
//
// Motors will differ in wiring. Buy motors that include
// a datasheet or a pin diagram. For example, my motor
// has a 6-pin connector with the wiring diagram shown
// below.
// 
// 6-pin Connector
// ===============================================
// | A      | NC | B      | C      | NC | D      |
// | Red    |    | Black  | Blue   |    | Green  |
// | B+     |    | A+     | B-     |    | A-     |
// | Pair 1 |    | Pair 2 | Pair 1 |    | Pair 2 |
// ===============================================
// wired as:
// | 1B     |    | 2B     | 1A     |    | 2A     |
// ===============================================
//
// This wiring results in
// 
//   Forward = Clockwise
//   Reverse = Counterclockwise
//
//*****************************************************
//*****************************************************

//
// Motor steps for 1 full revolution.
//
#define STEPS 200

//
// Define the microstep configuration. This depends on the
// values (HIGH or LOW) of the MSx pins on the A4988 board.
//
//  MS1   MS2   MS3   Microstep    MICROSTEP
//                    Resolution   Value
//  ========================================
//  LOW   LOW   LOW   Full step      1
//  HIGH  LOW   LOW   1/2 step       2
//  LOW   HIGH  LOW   1/4 step       4
//  HIGH  HIGH  LOW   1/8 step       8
//  HIGH  HIGH  HIGH  1/16 step     16
//
#define MICROSTEPS 16

//
// Define the number of seconds to
// pause between moves.
//
#define PAUSE_BETWEEN_MOVES 2

//
// Create the SpeedyStepper instance.
//
SpeedyStepper stepper;

void setup()
{
  //
  // Initialize the serial port.
  //
  Serial.begin(500000);

  //
  // Wait for serial port to connect.
  //
  while (!Serial) {}
  Serial.println("Serial port initialized.");

  //
  // Connect and configure the SpeedyStepper instance.
  //
  Serial.println("Configurating to stepper motor driver.");
  stepper.connectToPins(MOTOR_STEP_PIN, MOTOR_DIRECTION_PIN);

  //
  // Set the number of steps per revolution.
  //
  stepper.setStepsPerRevolution(STEPS * MICROSTEPS);

  //
  // Set the speed and acceleration rates for the stepper motor
  // 60 RPM (1 rotation per second).
  //
  stepper.setSpeedInRevolutionsPerSecond(1.0);
  stepper.setAccelerationInRevolutionsPerSecondPerSecond(1.0);
  Serial.println("Stepper motor driver configuration completed.");
  Serial.print("Connected to: "); Serial.println(MOTOR_NAME);
  
  //
  // Setup has completed.
  //
  Serial.println("Ready.");
}

void loop() {
  //
  // All moves are started at the motor's current position. The calls
  // to move the stepper will not return until the motion is complete.
  //
  Serial.println("Demonstrating relative moves.");
  demonstrateRelativeMoves();

  //
  // The motor's starting position is 0. A calls set a value that is based
  // on this starting point. The calls to move the stepper will not
  // return until the motion is complete.
  //
  Serial.println("Demonstrating absolute moves.");
  demonstrateAbsoluteMoves();

  //
  // The rotation has completed. pause for 5 seconds before
  // repeating the sequence.
  //
  Serial.println("Pausing for 5 seconds.");
  delay(5000);
}

void demonstrateRelativeMoves() {
  //
  // Rotate the motor in the forward direction one revolution
  // and pause.
  //
  Serial.println("Rotating 1 full forward turn.");
  stepper.moveRelativeInRevolutions(1.0);
  delay(PAUSE_BETWEEN_MOVES * 1000);

  //
  // Rotate the stepper in the opposte direction one
  // full revolution and pause.
  //
  Serial.println("Rotating 1 full reverse turn.");
  stepper.moveRelativeInRevolutions(-1.0);
  delay(PAUSE_BETWEEN_MOVES * 1000);

  //
  // Rotate the motor in the forward direction a half
  // revolution and pause.
  //
  Serial.println("Rotating 1/2 forward turn.");
  stepper.moveRelativeInRevolutions(.5);
  delay(PAUSE_BETWEEN_MOVES * 1000);
  
  //
  // Rotate the stepper in the opposite direction a
  // half revolution and pause.
  //
  Serial.println("Rotating 1/2 reverse turn.");
  stepper.moveRelativeInRevolutions(-.5);
  delay(PAUSE_BETWEEN_MOVES * 1000);
}

void demonstrateAbsoluteMoves() {
  //
  // Move the motor to position .500 and pause.
  //
  Serial.println("Moving to position .500.");
  stepper.moveToPositionInRevolutions(.500);
  delay(PAUSE_BETWEEN_MOVES * 1000);

  //
  // Move the motor to .650 and pause.
  //
  Serial.println("Moving to position .650.");
  stepper.moveToPositionInRevolutions(.650);
  delay(PAUSE_BETWEEN_MOVES * 1000);

  //
  // Move the motor to .765 and pause.
  //
  Serial.println("Moving to position .765.");
  stepper.moveToPositionInRevolutions(.765);
  delay(PAUSE_BETWEEN_MOVES * 1000);

  //
  // Move the motor to .085 and pause.
  //
  Serial.println("Moving to position .085.");
  stepper.moveToPositionInRevolutions(.085);
  delay(PAUSE_BETWEEN_MOVES * 1000);

  //
  // Move the motor to .160 and pause.
  //
  Serial.println("Moving to position .160.");
  stepper.moveToPositionInRevolutions(.160);
  delay(PAUSE_BETWEEN_MOVES * 1000);

  //
  // Move the motor to 0 and pause. The motor
  // should be back to the starting point.
  //
  Serial.println("Moving to position 0.");
  stepper.moveToPositionInRevolutions(0);
  delay(PAUSE_BETWEEN_MOVES * 1000);
}

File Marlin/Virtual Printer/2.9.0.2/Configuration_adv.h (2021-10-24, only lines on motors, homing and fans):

#define E0_AUTO_FAN_PIN -1
#define E1_AUTO_FAN_PIN -1
#define E2_AUTO_FAN_PIN -1
#define E3_AUTO_FAN_PIN -1
#define E4_AUTO_FAN_PIN -1
#define E5_AUTO_FAN_PIN -1
#define E6_AUTO_FAN_PIN -1
#define E7_AUTO_FAN_PIN -1
#define CHAMBER_AUTO_FAN_PIN -1
#define COOLER_AUTO_FAN_PIN -1
#define COOLER_FAN_PIN -1
#define HOMING_BUMP_MM      { 5, 5, 2 }       // (mm) Backoff from endstops after first bump
#define HOMING_BUMP_DIVISOR { 2, 2, 4 }       // Re-Bump Speed Divisor (Divides the Homing Feedrate)
#define QUICK_HOME                          // If G28 contains XY do a diagonal move first
#define MICROSTEP_MODES { 16, 16, 16, 16, 16, 16 } // [1,2,4,8,16]

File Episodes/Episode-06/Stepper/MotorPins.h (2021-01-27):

#ifndef MOTOR_PINS_H
#define MOTOR_PINS_H

// ***
// *** These are the pin assignments for the
// *** connection to the A4988 board.
// ***

#ifdef E-MOTOR
  #define MOTOR_NAME "E Motor"
  #define MOTOR_STEP_PIN 1
  #define MOTOR_DIRECTION_PIN 0
  #define MOTOR_EN 14
#endif

#ifdef Z-MOTOR
  #define MOTOR_NAME "Z Motor"
  #define MOTOR_STEP_PIN 3
  #define MOTOR_DIRECTION_PIN 2
  #define MOTOR_EN 26
#endif

#ifdef X-MOTOR
  #define MOTOR_NAME "X Motor"
  #define MOTOR_STEP_PIN 15
  #define MOTOR_DIRECTION_PIN 21
  #define MOTOR_EN 14
#endif

#ifdef Y-MOTOR
  #define MOTOR_NAME "Y Motor"
  #define MOTOR_STEP_PIN 22
  #define MOTOR_DIRECTION_PIN 23
  #define MOTOR_EN 14
#endif

#endif

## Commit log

2021-01-26 Uploaded files.
    [3DPB-Schematic-Episode-02.fzz, 3DPB-Schematic-Episode-04.fzz, 3DPB-Schematic-Episode-06.fzz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]
2021-01-26 Corrected wiring.
    [3DPB-Schematic-Episode-06.fzz]
2021-01-30 Updated wiring.
2021-01-31 Added PDF's
    [3DPB-Schematic-Episode-09.fzz]
2021-02-01 Added Marlin
    [Configuration.h, Configuration_adv.h]
2021-02-01 Added Marlin Images
2021-02-01 Added Marlin Config
    [Configuration.h, Configuration_adv.h]
2021-05-31 Changed to 2.0.7.2
    [Configuration.h, Configuration_adv.h]
2021-10-23 Updated to 2.0.9.2
    [Configuration.h, Configuration_adv.h]

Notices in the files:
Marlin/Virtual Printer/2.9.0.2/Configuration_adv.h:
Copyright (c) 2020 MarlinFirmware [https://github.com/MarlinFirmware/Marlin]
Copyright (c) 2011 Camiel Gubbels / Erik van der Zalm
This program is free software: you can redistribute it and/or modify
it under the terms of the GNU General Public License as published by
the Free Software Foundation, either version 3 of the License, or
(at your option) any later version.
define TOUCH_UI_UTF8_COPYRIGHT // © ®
